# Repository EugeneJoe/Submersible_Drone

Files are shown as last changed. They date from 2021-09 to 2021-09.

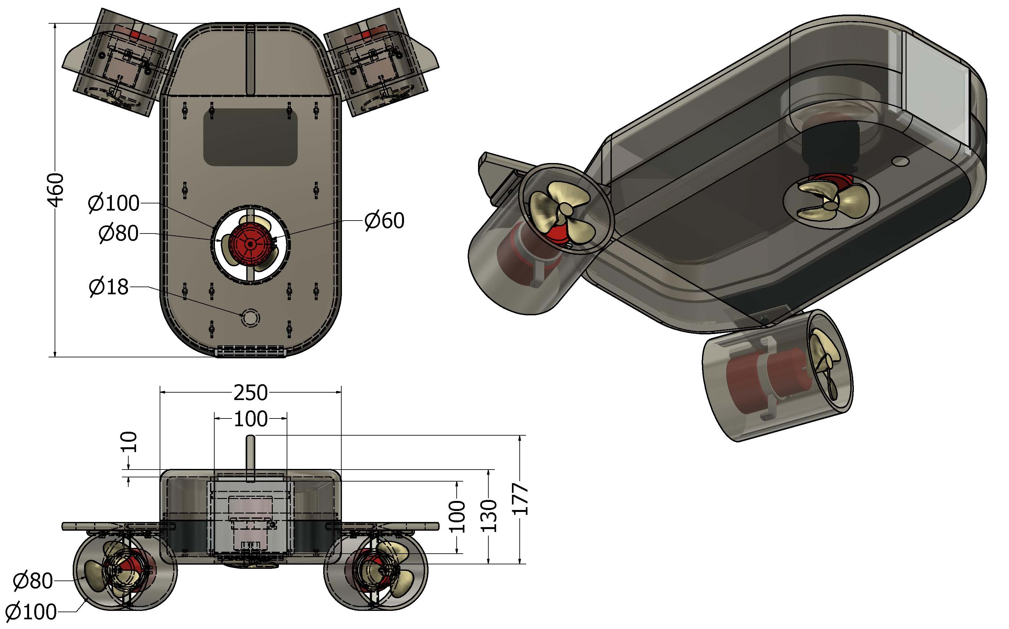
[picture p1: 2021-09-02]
Working_Drawings/JPG/Underwater ROV Assembly_Overall Dimensions.jpg

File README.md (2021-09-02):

# Submersible Drone Project

The files in this repository describe the different aspects that went into building our submersible, remote controlled drone. The drone was capable of underwater exploration through the use of a camera that sent back a live video feed of the submerged environment.
The different sections that went into the drone are:

1. An outer shell that is water-tight and housed all the components and positioned them appropriately.
2. Three motors from water pumps to provide vertical and horizontal thrust.
3. A raspberry pi controller through which the live video feed was transmitted and
propulsion signals were sent.
4. An arduino controller that received signals from the raspberry pi and drove the motors
through motor controller chips.
5. A raspberry pi camera module to capture video and transmit it back to the user. This could be viewed from a laptop.

The Final Report document contains a detailed report of how we went about designing and building the drone.

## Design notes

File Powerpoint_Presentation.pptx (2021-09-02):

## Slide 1

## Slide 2

Introduction: Objectives

Main Objective
  - Design and fabricate a hydrodynamic submersible vehicle capable of manoeuvring underwater environments and capturing videos and images

Specific Objectives
In order to achieve the above main objective, the following specific objectives must be satisfied:
1. To design and fabricate a water-tight hull of the ROV, keeping in mind hydrodynamics and strength of the mechanical design.
2. To design and fabricate the propulsion and pitch control system of the ROV.
3. To design the power delivery circuit to the electrical components in the ROV.
4. To design and implement the algorithm that coordinates the functioning of the ROV.
5. To test the operation and performance of the ROV system modules, and eventually the entire system operation with the modules working in tandem.

## Production Plan

Week | Tasks/ Activities | Materials Required | Special equipment | Simultaneous/ Concurrent activities | Status/ Remarks
5 | Assembly of live stream equipment Testing the live video stream | Raspberry pi camera module Raspberry pi microcontroller Display unit CAT 6 Cable | | | Complete
6 | Assembly of the power circuit: Acquisition of power supply unit Acquisition of terminal block and buck converter. Acquisition of CAT 6 cable Assembling the above components | CAT 6 Cable Power supply unit Buck converter | | | Power supply + Buck Converter acquired. Acquisition of cables underway.

## Production Plan

Week | Tasks/ Activities | Materials Required | Special equipment | Simultaneous/ Concurrent activities | Status/ Remarks
7 | Modification of Bilge pumps: Marking the housing where it needs to be cut. Cutting around the entire impeller housing being careful not to cut to deep into the motor casing, then discarding it. Prying the impeller off to expose the motor shaft. | 3No. Bilge pumps | Hobby Saw | | Complete
8 | Assembly of the motor control circuit Acquisition of materials required Connection to power circuit Testing the motor control for propulsion and pitch motors | Modified Bilge Pump Motors Dual channel H-bridge DC motor drivers Raspberry pi Microcontroller Jumper cables | | | Motor drivers – acquired.

## Production Plan

Week | Tasks/ Activities | Materials Required | Special equipment | Simultaneous/ Concurrent activities | Status/ Remarks
9 | 3D Print the mechanical structure of the ROV - Outer hull, propeller shrouds, propellers, motor support brackets. | Polyactic Acid (PLA) | 3D Printer | | Ongoing
10 | Machining of camera sight glass | Glass (108 × 106 × 3 mm) | | | Complete
11 | Assembly of the different components of the mechanical structure | Acetone / Epoxy / Cyanoacrylate Superglue / Solvent cement M5 × 10 set screws (6No.) M5 × 12 set screws (8No.) M5 Lock nuts (9No.) | | i) Fine tuning motor control
12 | Test of the complete U-ROV assembly and fine tuning its operation

## Methodology – Revised Mechanical Design - Exploded View

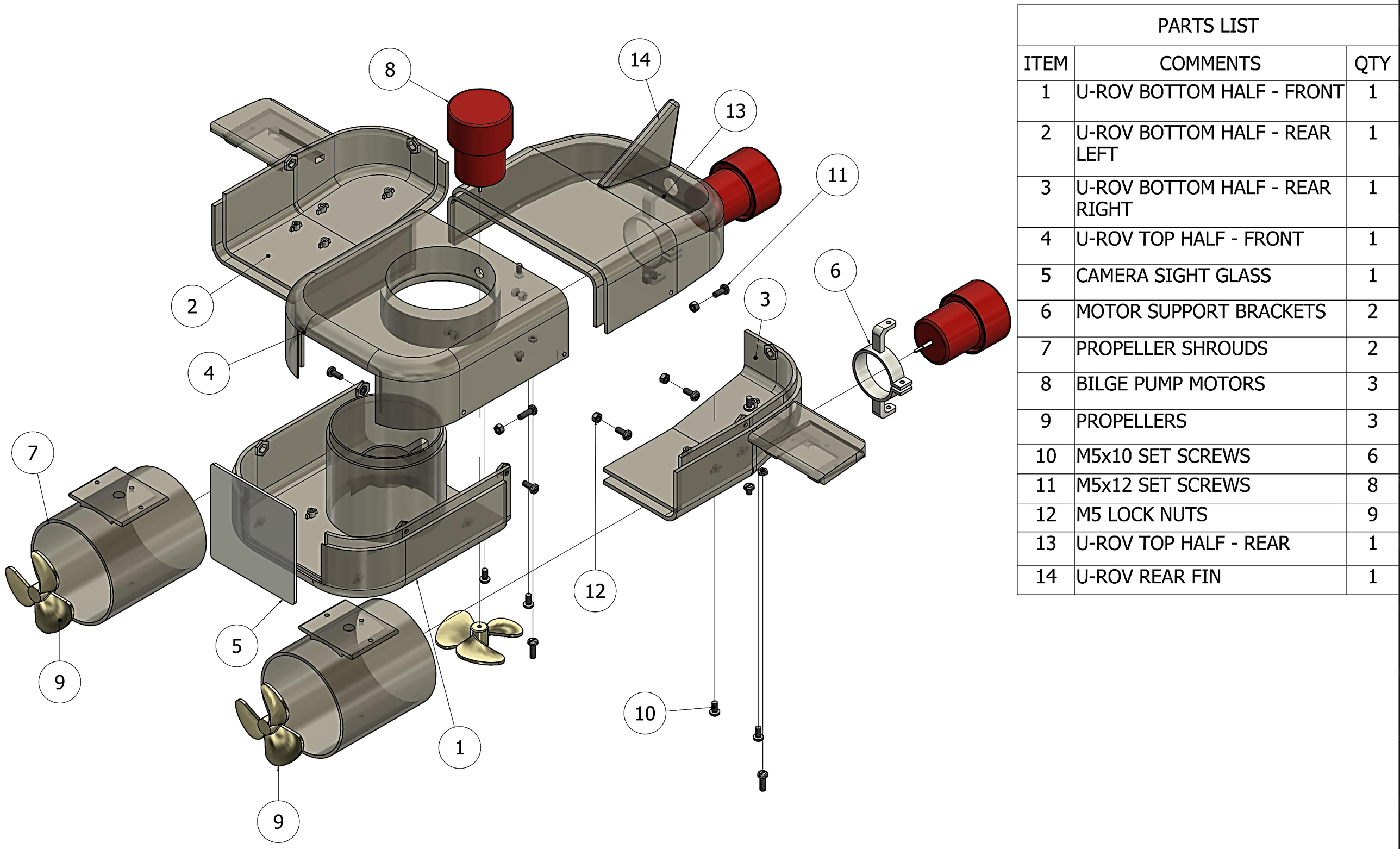
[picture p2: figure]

## Methodology – Flowchart

START

LIVESTREAM AUTOMATICALLY ACTIVATED

PITCH THRUSTER TRIGGERED

DESIRED DEPTH REACHED?

PITCH THRUSTER DEACTIVATED

FORWARD (F) / BACKWARD (B) MOTION?

c

F

B

NO

THRUSTER CLOCKWISE MOTION TRIGGERED

THRUSTER COUNTERCLOCKWISE MOTION TRIGGERED

YES

A

## Methodology – Flowchart

A

B

TURN LEFT(L) / RIGHT(R)?

RESURFACE?

PITCH THRUSTER REVERSED

END

N

C

L

R

Y

LEFT THRUSTER SPEED DECREASED

RIGHT THRUSTER SPEED DECREASED

B

## Control Module

  - Gamepad connected to laptop to which it sends signals based on user input.
  - Signal sent from joystick includes:
    - Direction of motion i.e ‘F’ for Forward, ‘R’ for Right.
    - Speed value to be passed to motor as PWM value:
      - Joystick input range (0-1) mapped to PWM values (0-255)
  - Laptop connected to Raspberry Pi as client with Pi acting as server.
  - Raspberry Pi receives Gamepad signal from laptop.
  - Raspberry pi sends signal to Arduino through Serial Connection.
  - Arduino actuates motors based on received signal.

## Budget

S/No | Item | Specifications | Qty | Units | Material | Estimated Unit Cost | Total Cost
1 | Raspberry pi camera module** | | 1 | Pieces | | 3,500 | 3,500*
2 | Raspberry pi** | | 1 | Pieces | | 6,000 | 6,000*
3 | Electric Bilge Pump | 1100 GPH, 12V, 3A | 3 | Pieces | | 1,836 | 5,508
4 | DC motor drivers | 3V-36V, 15A Dual Channel H-bridge | 2 | Pieces | | 1,838 | 3,676
5 | CAT6 cable | | 6 | Length (m) | | 70 | 420
6 | CAT6 cable end connectors | | 2 | Pieces | | 10 | 20
7 | Buck converter | LM2596HVS – 60V, 3A | 1 | Pieces | | 400 | 400

## Budget

S/No. | Item | Specifications | Qnty | Units | Material | Estimated Unit Cost | Total Cost
8 | LED Ring Lights | 61mm OD, 52mm ID | 1 | Pieces | | 1,707 | 1,707
9 | Set screws | M5×10 | 6 | Pieces | | 10 | 60
10 | Set screws | M5×12 | 8 | Pieces | | 10 | 80
11 | Fuse | 10A | 3 | Pieces | | 130 | 390
12 | Glass | 106mm × 108mm × 3 mm | 1 | Pieces | | 200 | 200
13 | Waterproof Cable Glands | PG7 (12.5 mm OD), PG13.5 (20.4mm OD) | 4 | Pieces | | 150 | 600
14 | 3D Printing | | 1 | Item | PLA | 20,000 | 20,000
Total Estimated Cost | | | | | | | 33,061
Subtotal Currently Spent | | | | | | | 20,311

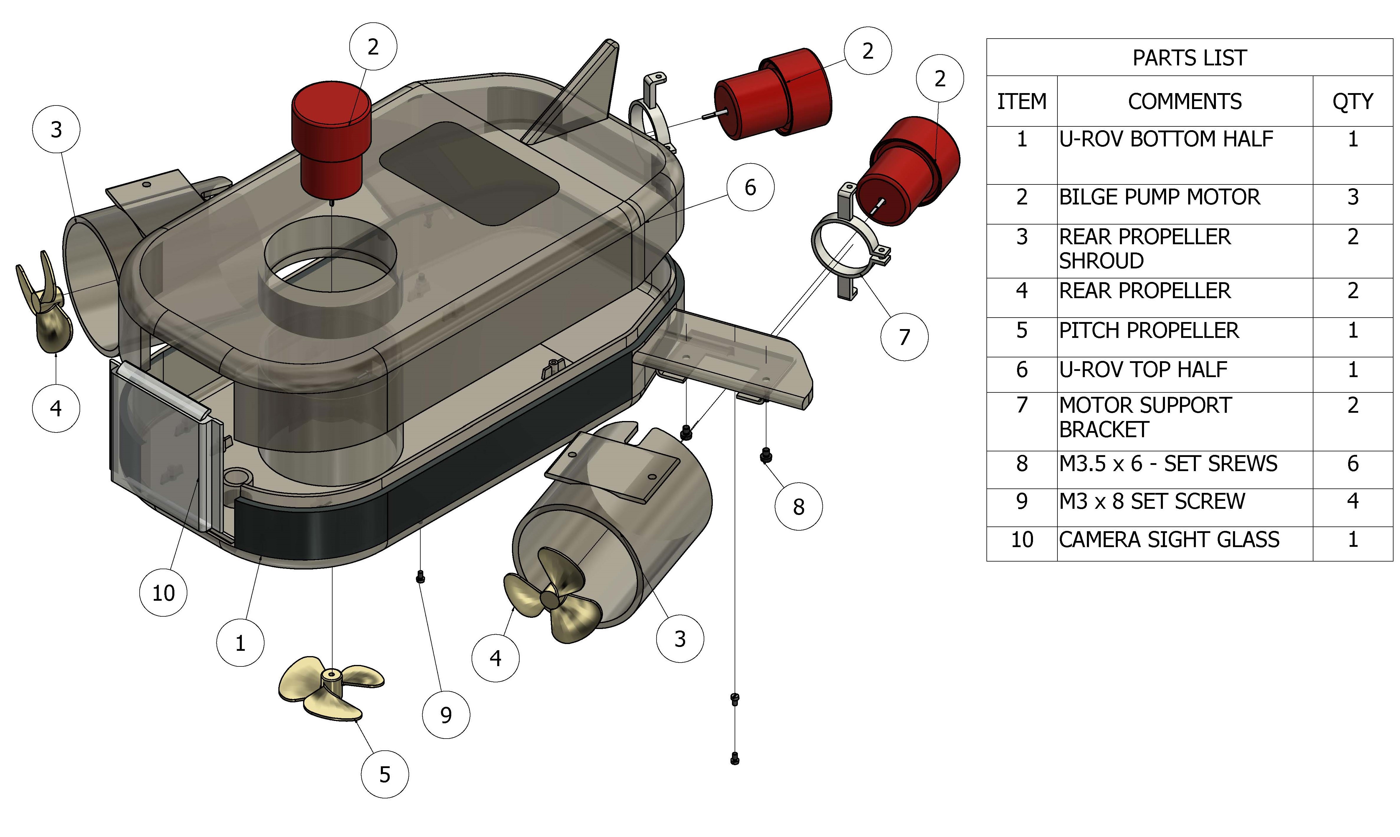
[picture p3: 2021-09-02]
Working_Drawings/PDF + DWG/EXPLODEDVIEW2.jpg

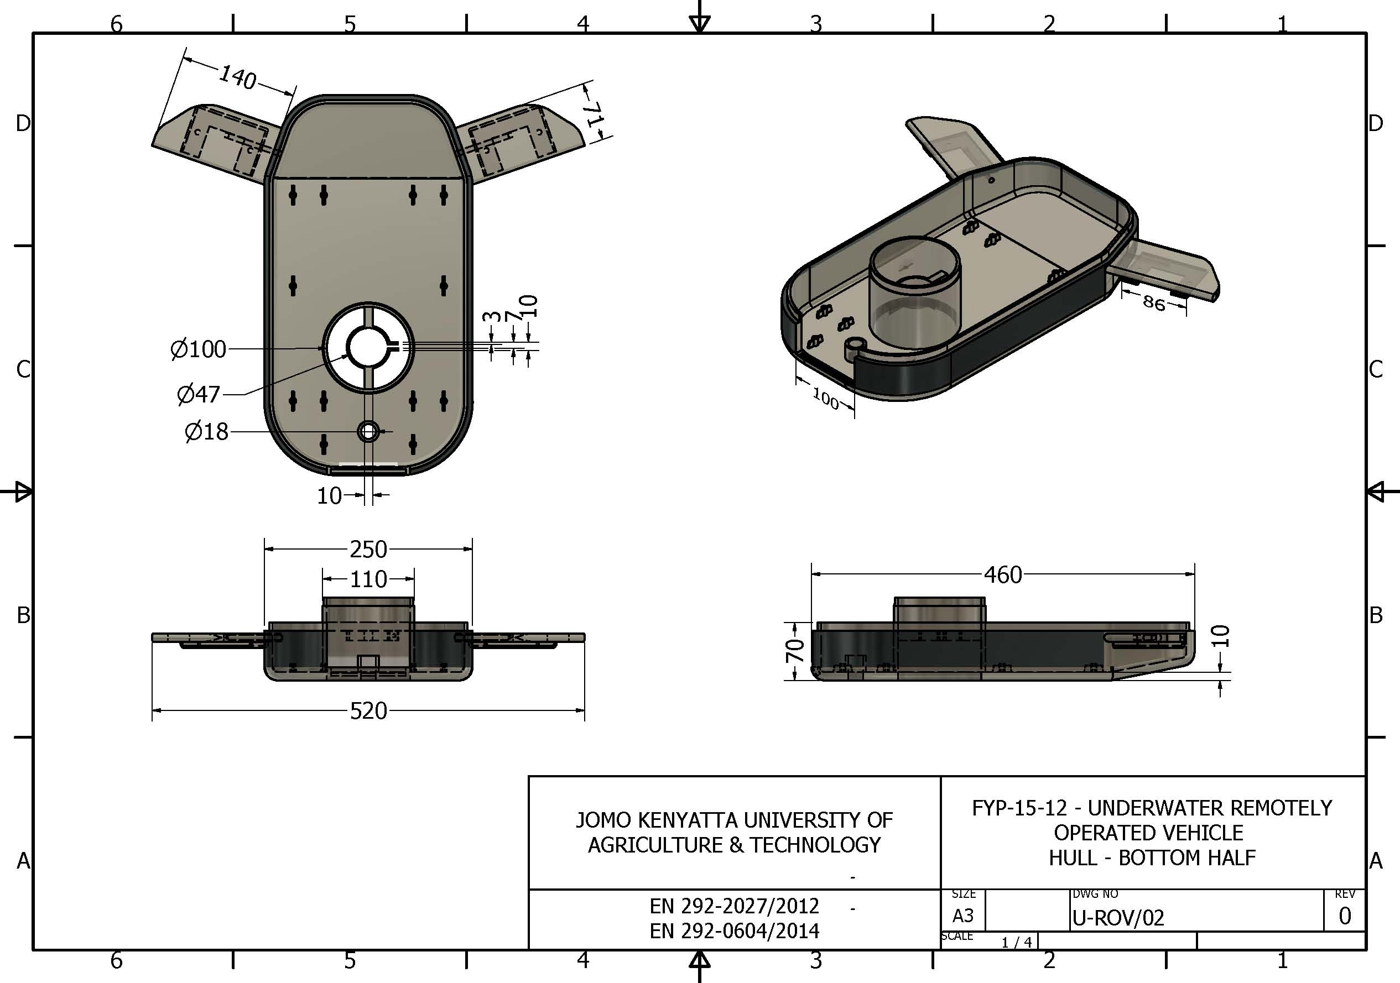
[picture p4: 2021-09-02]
Working_Drawings/PDF + DWG/HULL - BOTTOM HALF.jpg

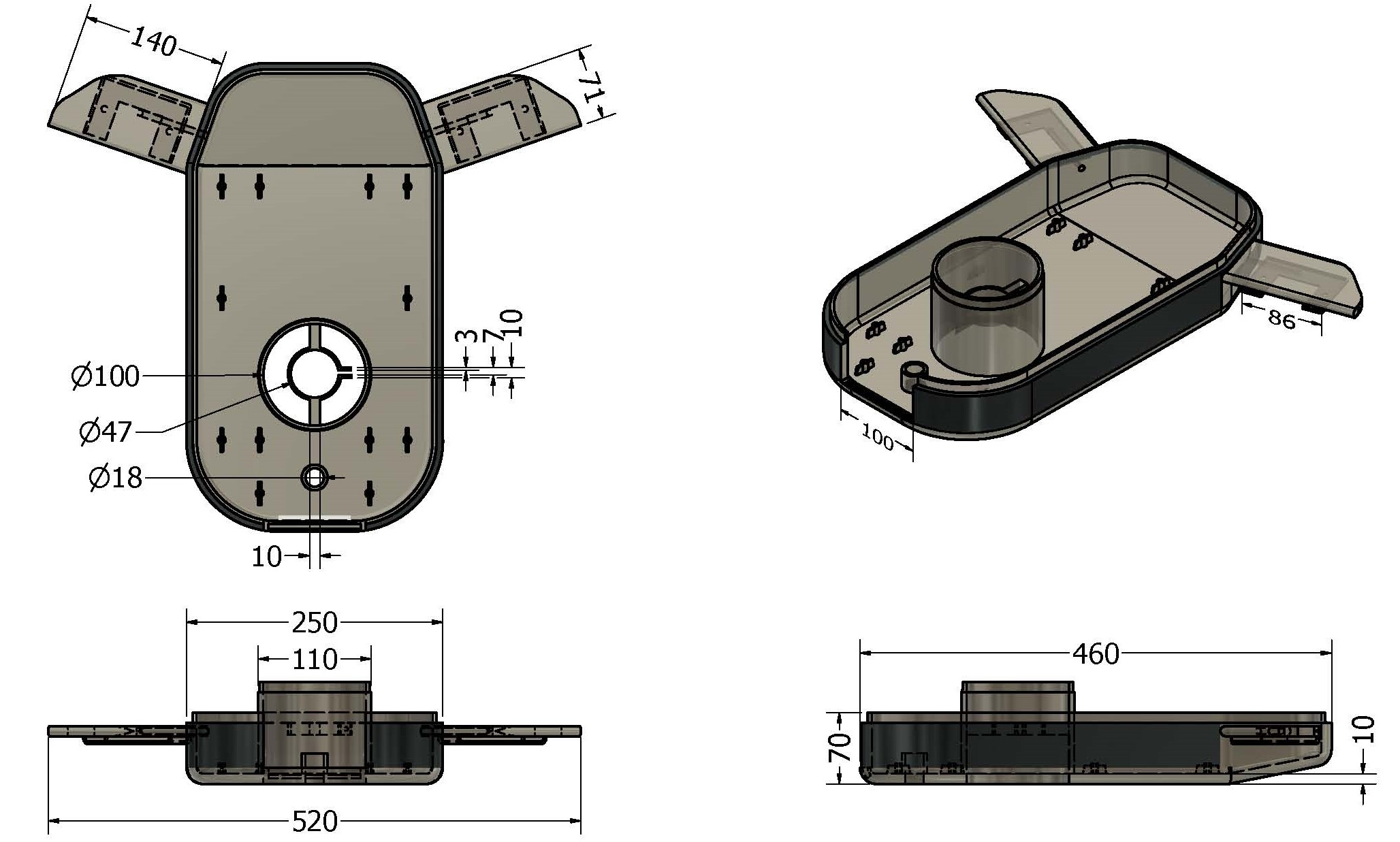
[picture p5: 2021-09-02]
Working_Drawings/JPG/U-ROV_Hull_BottomHalf3.0.jpg

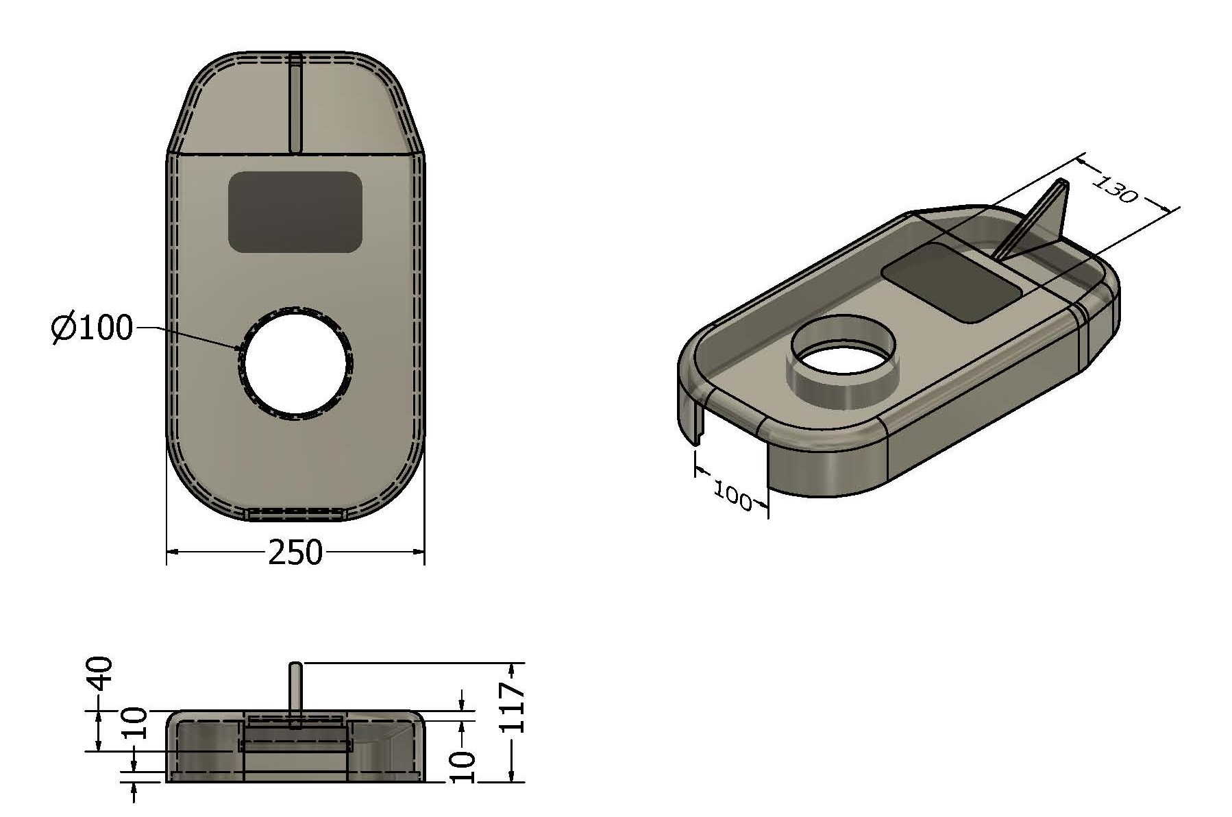
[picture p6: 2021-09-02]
Working_Drawings/JPG/U-ROV_Hull_Top Half3.0.jpg

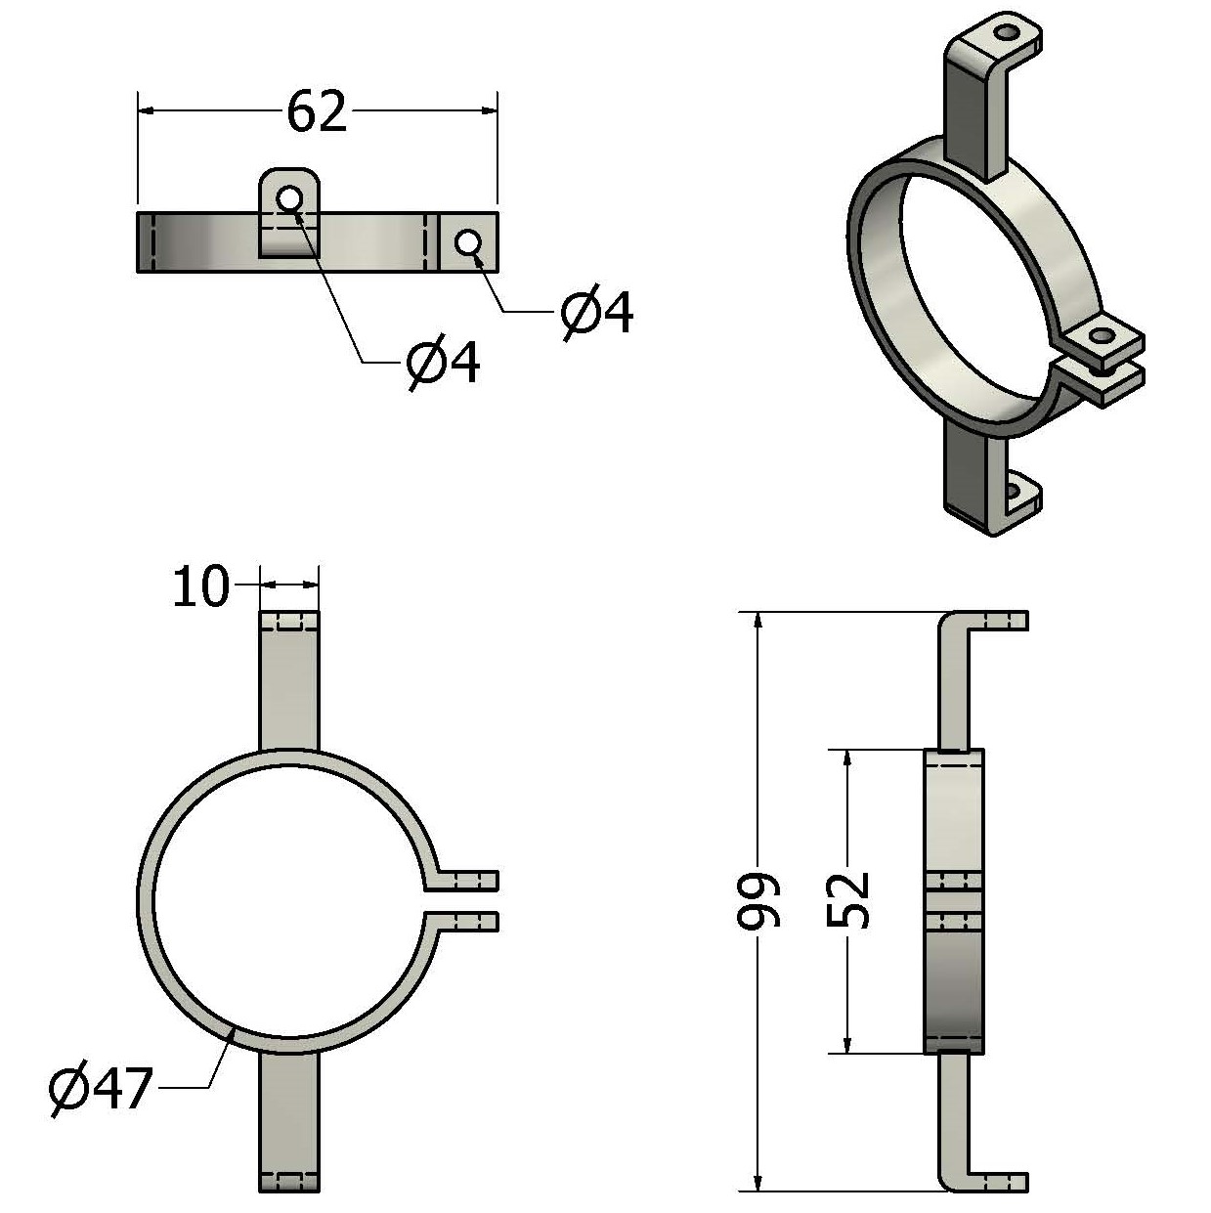
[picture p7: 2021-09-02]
Working_Drawings/JPG/SupportBracket_v2_BilgePumpMotor.jpg

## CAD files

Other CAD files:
Working_Drawings/PDF + DWG/U-ROV_Assembly_PartsLabelled.dwg
Working_Drawings/PDF + DWG/Underwater ROV Assembly_Overall Dimensions.dwg
Working_Drawings/PDF + DWG/U-ROV_Assembly_Exploded_WorkingDrawing-1.dwg
Working_Drawings/PDF + DWG/ROV Hull_Top Half 3.0.dwg
Working_Drawings/PDF + DWG/ROV Hull_Bottom Half 3.0.dwg
Working_Drawings/PDF + DWG/SupportBracket_v2_BilgePumpMotor.dwg
Working_Drawings/PDF + DWG/Propeller_Shroud.dwg
Working_Drawings/PDF + DWG/Rear Thruster 2.0.dwg
Working_Drawings/OldVersions/Underwater ROV Assembly_Overall Dimensions.0001.dwg
Working_Drawings/OldVersions/U-ROV_Assembly_Exploded_WorkingDrawing-1.0004.dwg
Working_Drawings/PDF + DWG/OldVersions/U-ROV_Assembly_Exploded_WorkingDrawing-1.0007.dwg
Working_Drawings/PDF + DWG/OldVersions/Underwater ROV Assembly_Overall Dimensions.0005.dwg
Working_Drawings/PDF + DWG/OldVersions/U-ROV_Assembly_PartsLabelled.0005.dwg
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

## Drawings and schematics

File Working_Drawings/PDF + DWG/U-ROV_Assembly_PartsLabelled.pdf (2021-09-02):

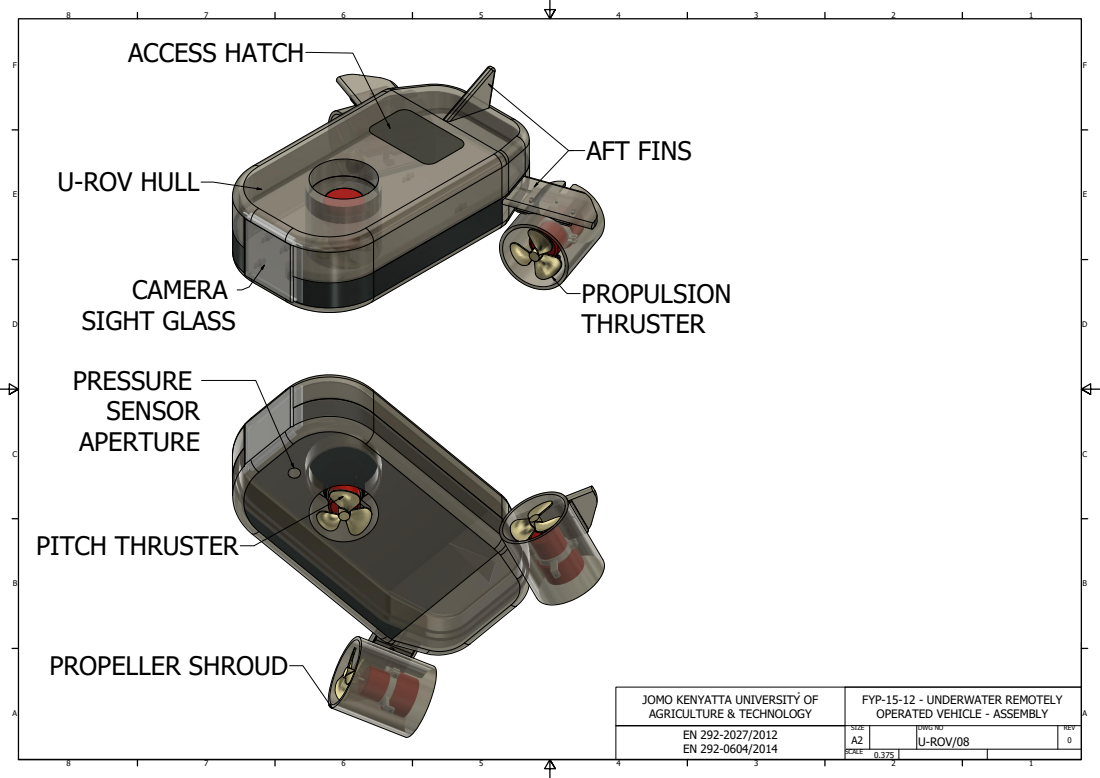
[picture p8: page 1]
U-ROV HULL; ACCESS HATCH; PITCH THRUSTER; SIGHT GLASS; AFT FINS; PROPELLER SHROUD

JOMO KENYATTA UNIVERSITY OF AGRICULTURE & TECHNOLOGY | FYP-15-12 - UNDERWATER REMOTELY OPERATED VEHICLE - ASSEMBLY

EN 292-2027/2012 EN 292-0604/2014 | SIZE A2 | DWG NO U-ROV/08 | REV 0

SCALE 0.375

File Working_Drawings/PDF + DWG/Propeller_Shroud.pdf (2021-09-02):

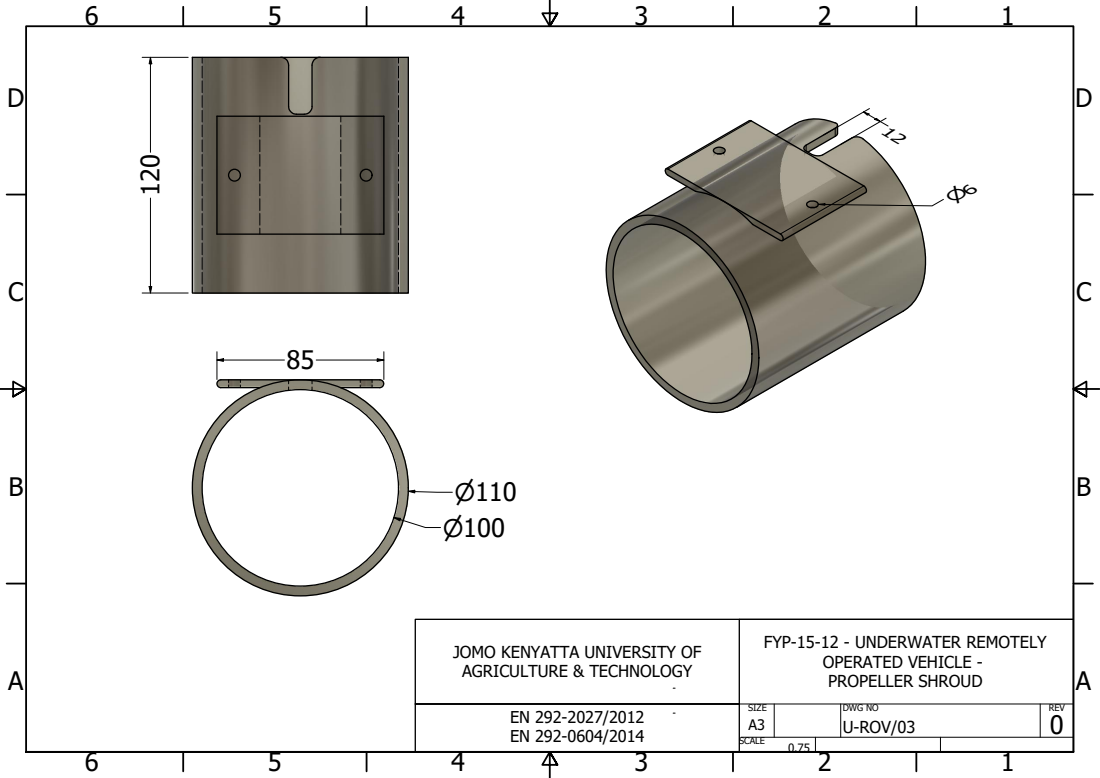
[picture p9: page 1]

JOMO KENYATTA UNIVERSITY OF AGRICULTURE & TECHNOLOGY | FYP-15-12 - UNDERWATER REMOTELY OPERATED VEHICLE -PROPELLER SHROUD

EN 292-2027/2012 EN 292-0604/2014 | SIZE A3 | DWG NO U-ROV/03 | REV 0

SCALE 0.75

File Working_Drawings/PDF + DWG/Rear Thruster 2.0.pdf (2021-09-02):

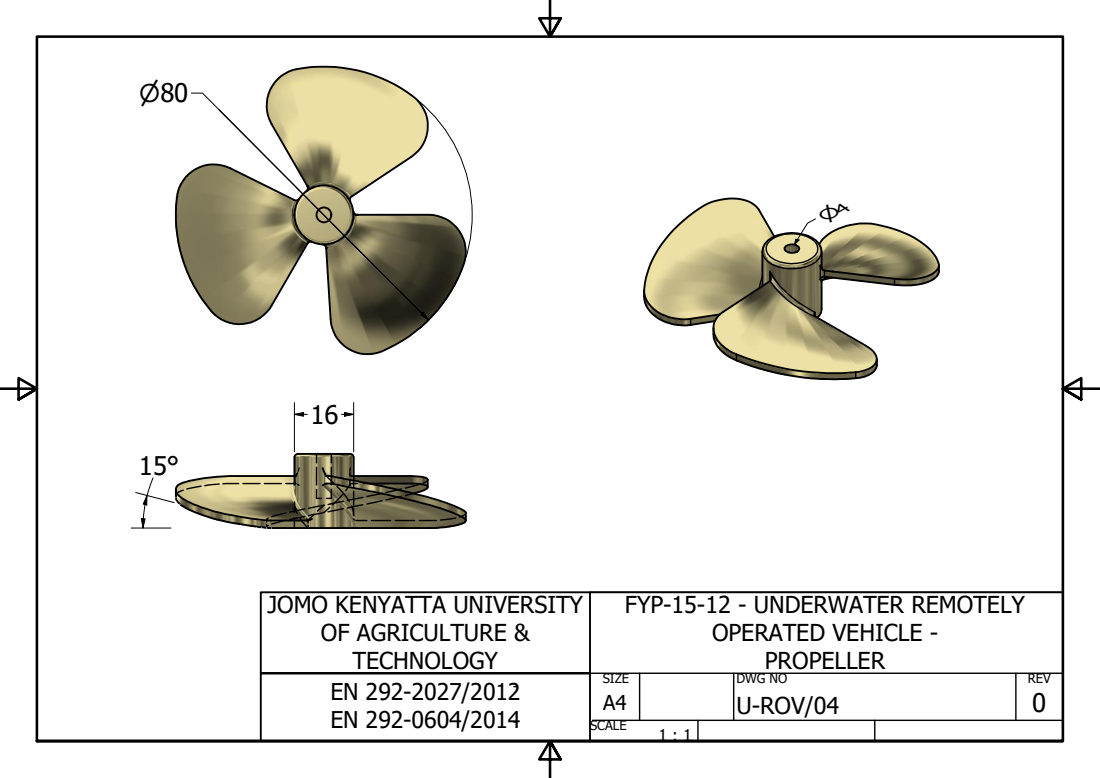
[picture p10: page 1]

JOMO KENYATTA UNIVERSITY OF AGRICULTURE & TECHNOLOGY | FYP-15-12 - UNDERWATER REMOTELY OPERATED VEHICLE -PROPELLER

EN 292-2027/2012 EN 292-0604/2014 | SIZE A4 | DWG NO U-ROV/04 | REV 0

SCALE 1 : 1

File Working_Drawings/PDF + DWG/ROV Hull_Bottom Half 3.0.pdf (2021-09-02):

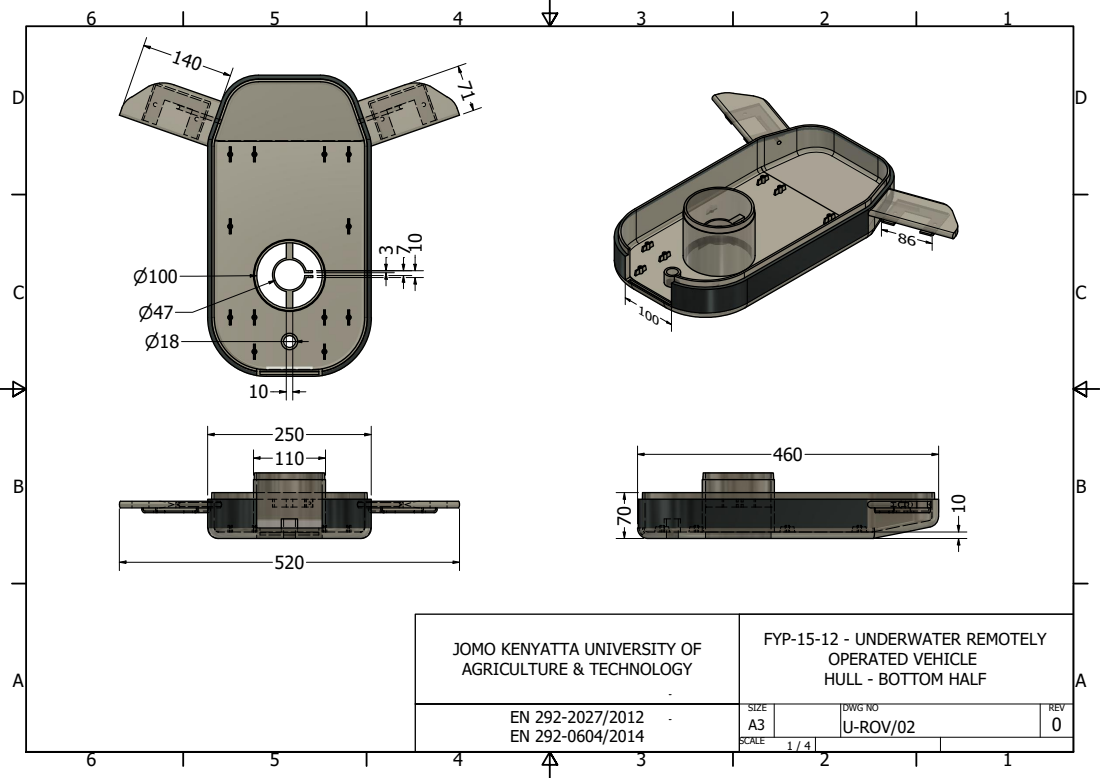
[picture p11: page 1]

JOMO KENYATTA UNIVERSITY OF AGRICULTURE & TECHNOLOGY | FYP-15-12 - UNDERWATER REMOTELY OPERATED VEHICLE HULL - BOTTOM HALF

EN 292-2027/2012 EN 292-0604/2014 | SIZE A3 | DWG NO U-ROV/02 | REV 0

SCALE 1 / 4

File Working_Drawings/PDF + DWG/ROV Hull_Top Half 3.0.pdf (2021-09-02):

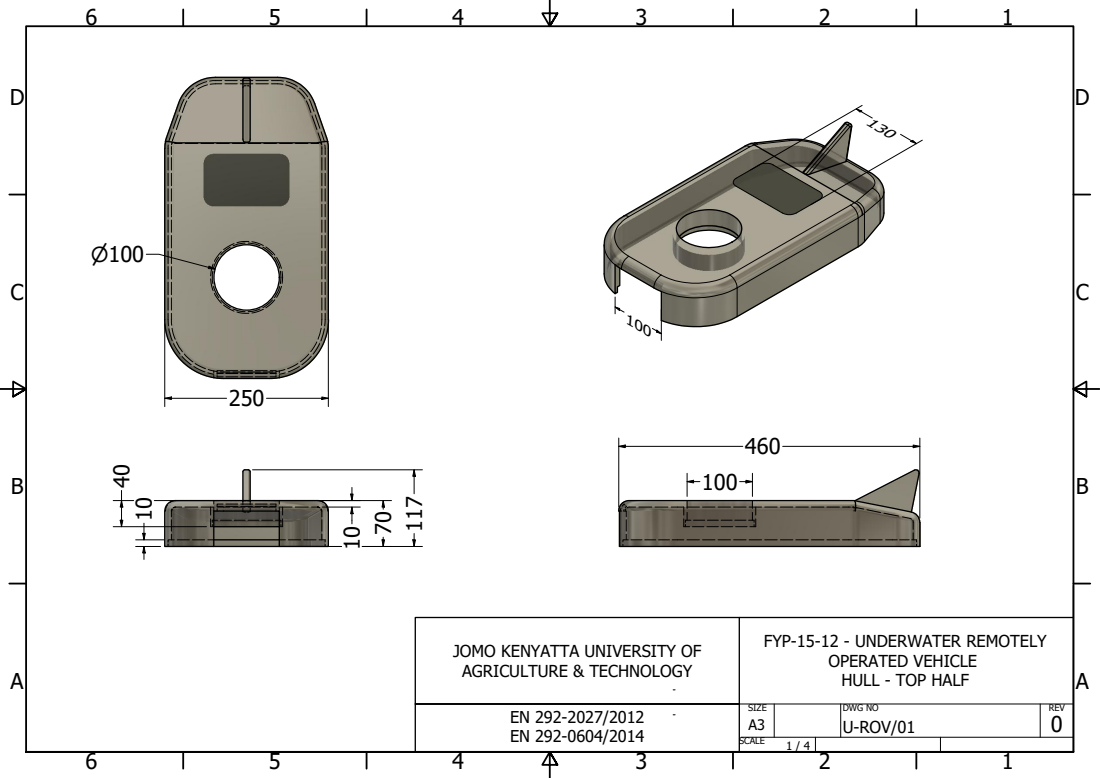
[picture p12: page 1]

JOMO KENYATTA UNIVERSITY OF AGRICULTURE & TECHNOLOGY | FYP-15-12 - UNDERWATER REMOTELY OPERATED VEHICLE HULL - TOP HALF

EN 292-2027/2012 EN 292-0604/2014 | SIZE A3 | DWG NO U-ROV/01 | REV 0

SCALE 1 / 4

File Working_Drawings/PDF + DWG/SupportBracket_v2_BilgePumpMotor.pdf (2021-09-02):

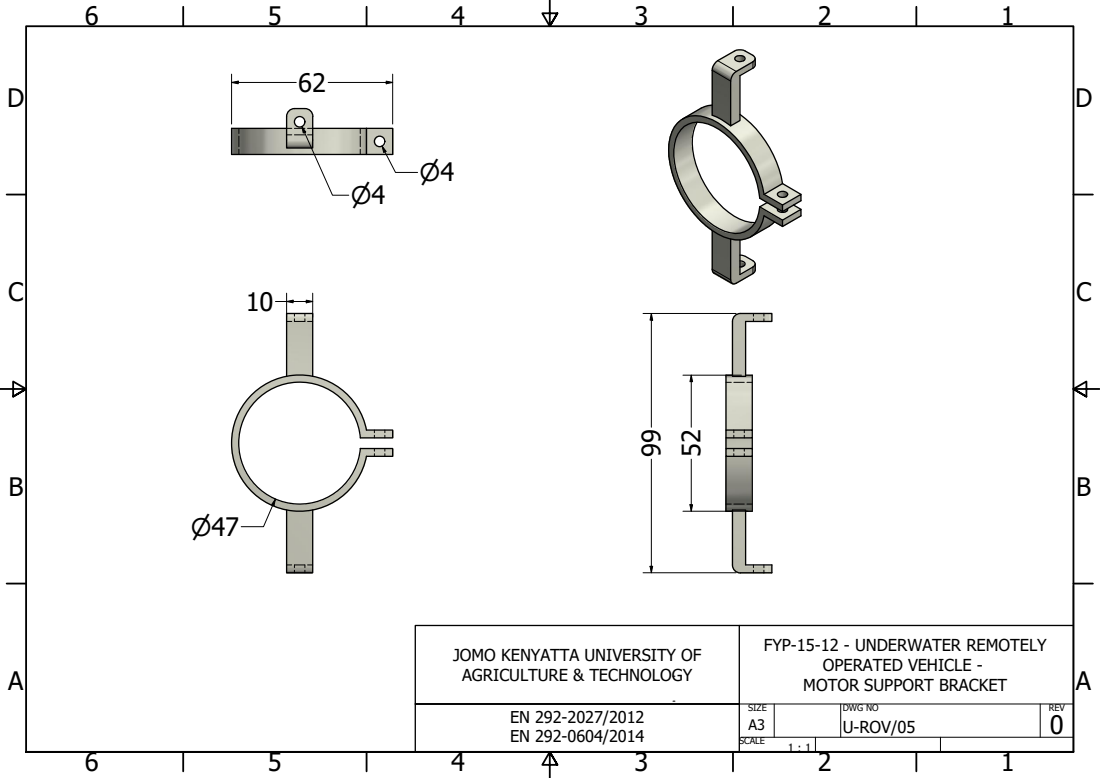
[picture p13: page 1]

JOMO KENYATTA UNIVERSITY OF AGRICULTURE & TECHNOLOGY | FYP-15-12 - UNDERWATER REMOTELY OPERATED VEHICLE -MOTOR SUPPORT BRACKET

EN 292-2027/2012 EN 292-0604/2014 | SIZE A3 | DWG NO U-ROV/05 | REV 0

SCALE 1 : 1

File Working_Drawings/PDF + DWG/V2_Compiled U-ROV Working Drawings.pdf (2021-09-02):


JOMO KENYATTA UNIVERSITY OF AGRICULTURE & TECHNOLOGY | FYP-15-12 - UNDERWATER REMOTELY OPERATED VEHICLE HULL - TOP HALF

EN 292-2027/2012 | SIZE A3 | DWG NO U-ROV/01 | REV

SCALE 1 / 4


JOMO KENYATTA UNIVERSITY OF AGRICULTURE & TECHNOLOGY | FYP-15-12 - UNDERWATER REMOTELY OPERATED VEHICLE HULL - BOTTOM HALF

SIZE | DWG NO | REV


JOMO KENYATTA UNIVERSITY OF AGRICULTURE & TECHNOLOGY | FYP-15-12 - UNDERWATER REMOTELY OPERATED VEHICLE -PROPELLER SHROUD

SIZE | DWG NO | REV


JOMO KENYATTA UNIVERSITY OF AGRICULTURE & TECHNOLOGY | FYP-15-12 - UNDERWATER REMOTELY OPERATED VEHICLE -PROPELLER

EN 292-2027/2012 | SIZE A4 | DWG NO U-ROV/04 | REV 0


JOMO KENYATTA UNIVERSITY OF AGRICULTURE & TECHNOLOGY | FYP-15-12 - UNDERWATER REMOTELY OPERATED VEHICLE -MOTOR SUPPORT BRACKET

SIZE | DWG NO | REV

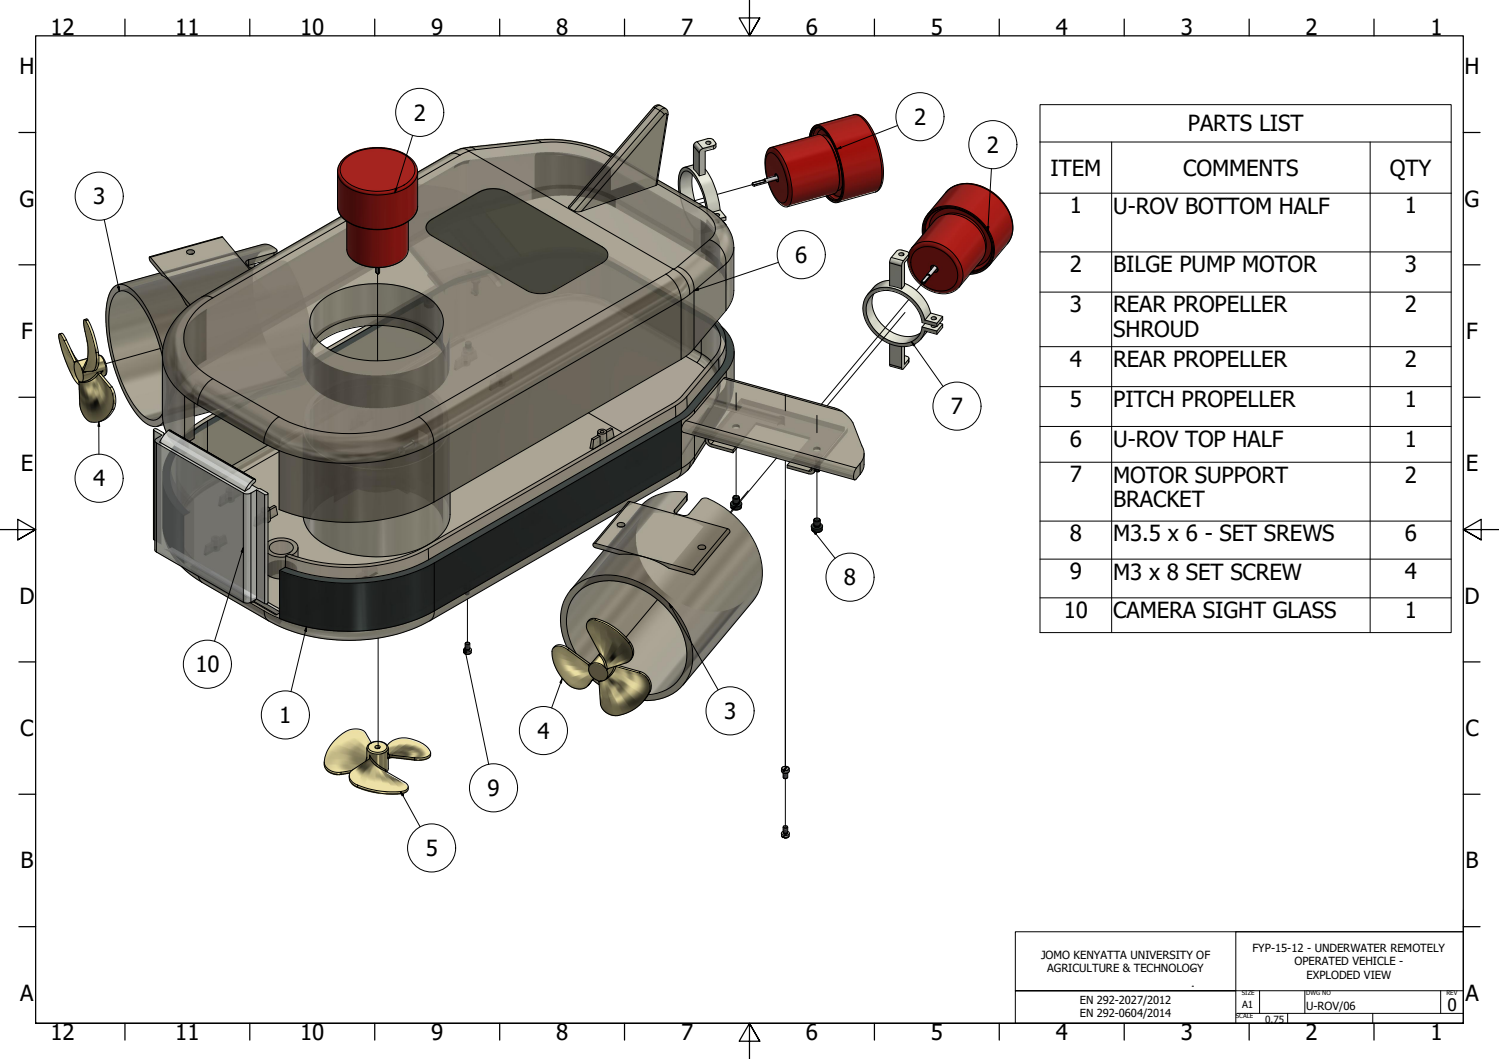
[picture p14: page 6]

I T E M | C O M M E N T S | Q TY
1 | U -R O V B O TT O M H A L F | 1

2 | B I L G E P U M P M O T O R | 3
34 | R E A R P R O P E L L E R S H R O U D | 2

R E A R P R O P E L L E R | 2
5 | P I T C H P R O P E L L E R | 1
6 | U -R O V T O P H A L F | 1
78 | M O T O R S U P P O RT B RA C K E T | 2

M 3 . 5 x 6 -S E T S R E W S | 6
9 | M 3 x 8 S E T S C R E W | 4
1 0 | C A M E RA S I G H T G LA S S | 1

J O M O K E N YATTA U N I V E R S I TY O F A G R I C U L T U R E & T E C H N O L O G Y | FY P -1 5 -1 2 -U N D E RW AT E R R E M O T E LY O P E RAT E D V E H I C L E -E X P L O D E D V I E W

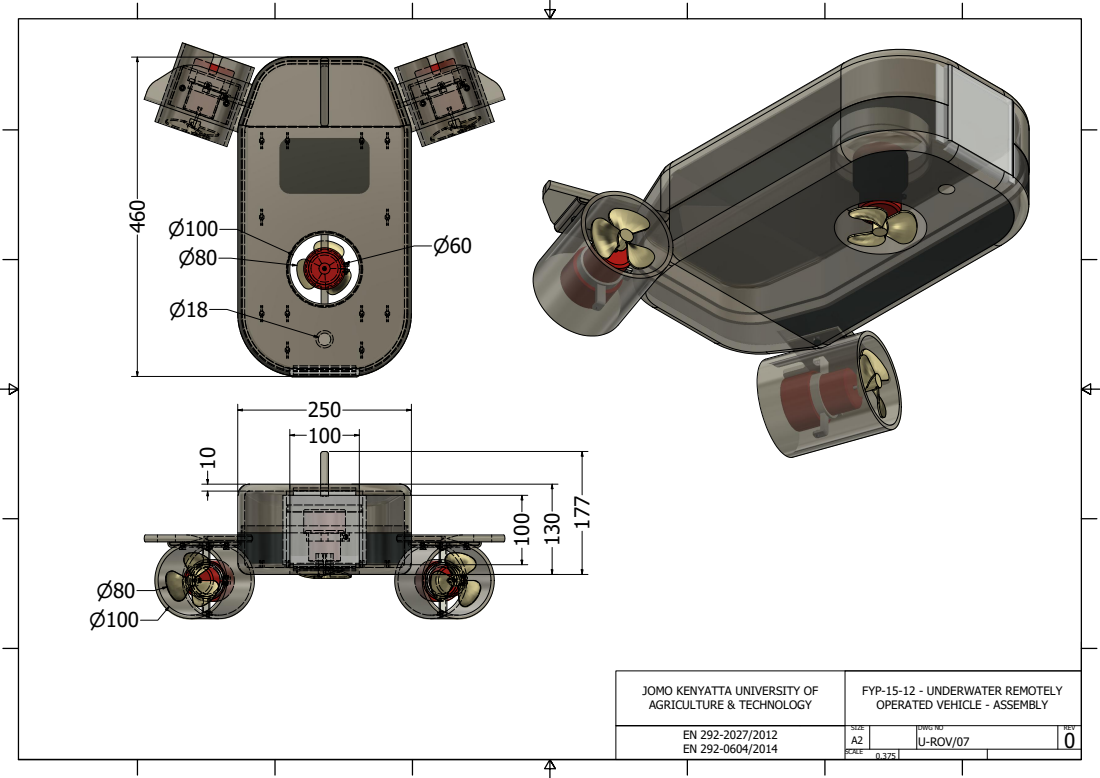
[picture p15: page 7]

JOMO KENYATTA UNIVERSITY OF AGRICULTURE & TECHNOLOGY | FYP-15-12 - UNDERWATER REMOTELY OPERATED VEHICLE - ASSEMBLY

SIZE | DWG NO | REV

U-ROV HULL; ACCESS HATCH; PITCH THRUSTER; SIGHT GLASS; AFT FINS; PROPELLER SHROUD

JOMO KENYATTA UNIVERSITY OF AGRICULTURE & TECHNOLOGY | FYP-15-12 - UNDERWATER REMOTELY OPERATED VEHICLE - ASSEMBLY

SIZE | DWG NO | REV

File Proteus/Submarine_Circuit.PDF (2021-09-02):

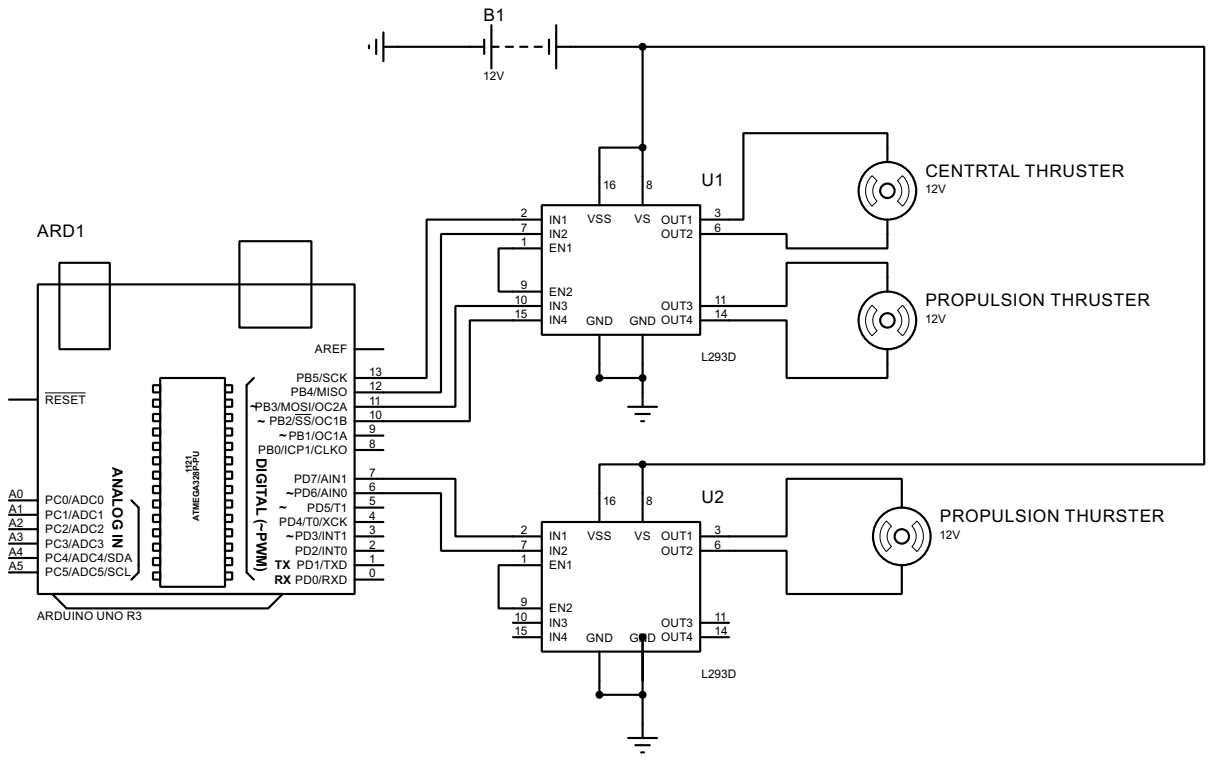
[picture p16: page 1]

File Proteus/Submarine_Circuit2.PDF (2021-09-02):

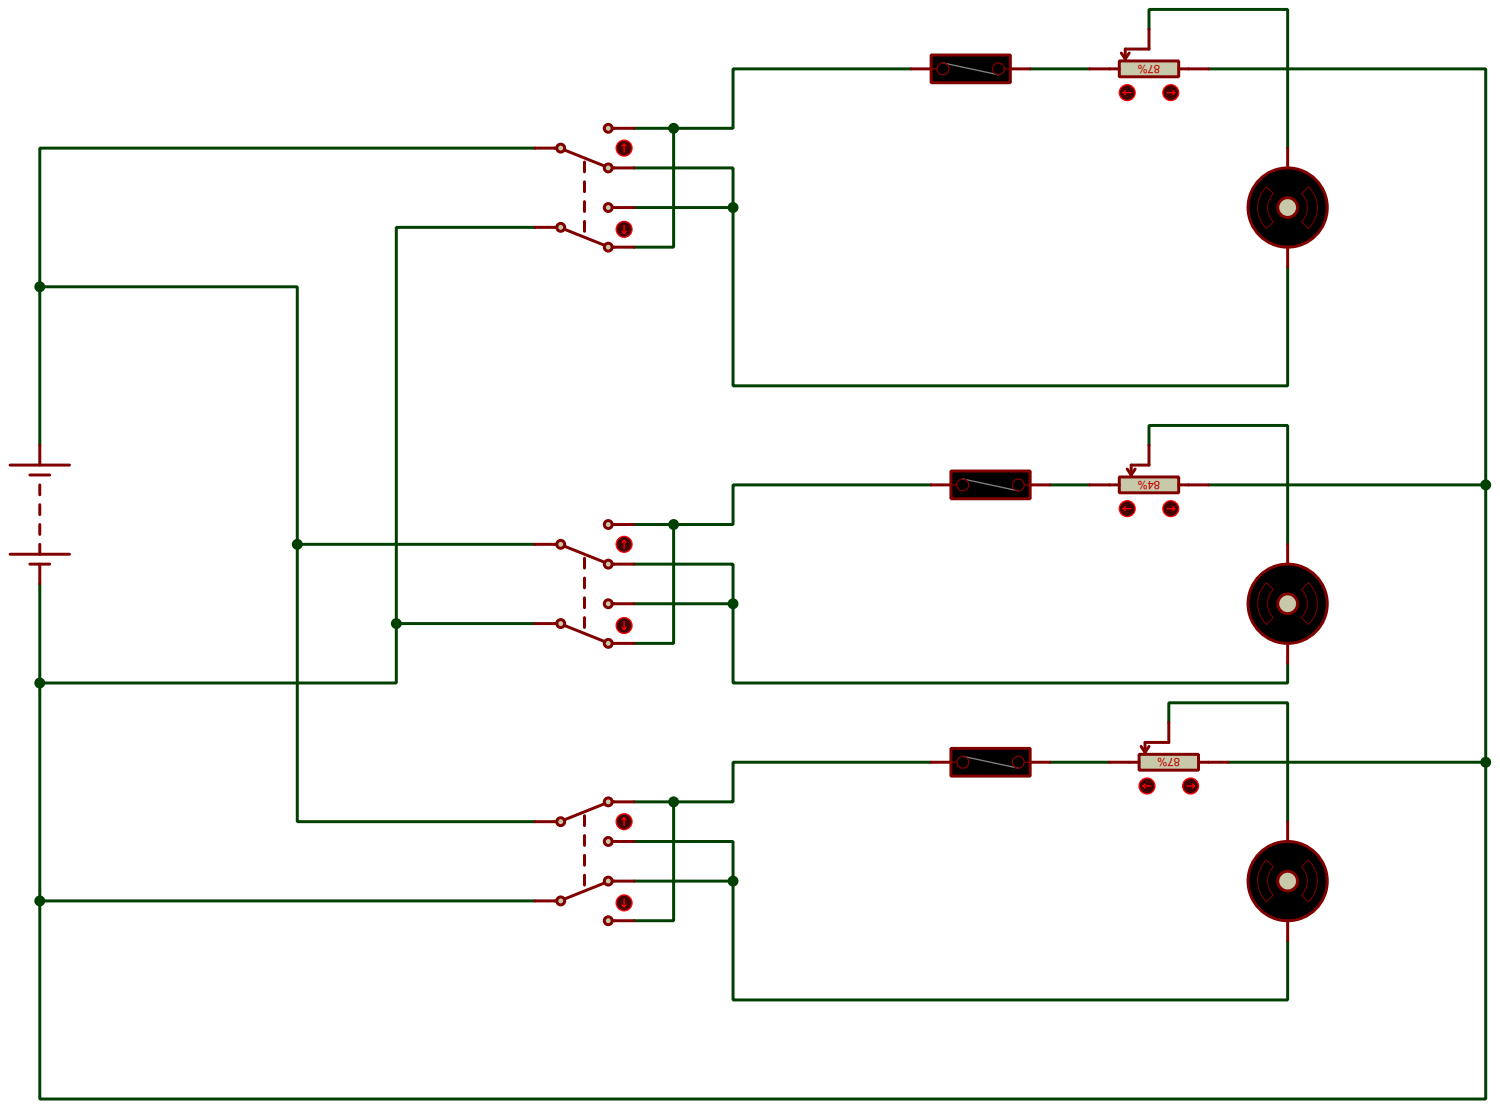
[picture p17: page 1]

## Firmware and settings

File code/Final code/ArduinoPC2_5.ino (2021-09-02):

//Enable Driver 2
int ENABLE1 = 8;
int ENABLE3 = 13;

//Motor1
int DIR1 = 9;
int PWM1 = 10;

//Motor 2
int DIR2 = 7;
int PWM2 = 6;

//Motor 3
int DIR3 = 12;
int PWM3 = 11;

//Input Read variables
const byte buffSize = 40;
char inputBuffer[buffSize];
const char startMarker = '<';
const char endMarker = '>';
byte bytesRecvd = 0;
boolean readInProgress = false;
boolean newDataFromPC = false;

char messageFromPC[buffSize] = {0};
char messageFromPC2[buffSize] = {0};
int newFlashInterval = 0;
int PWM_P = 0;
int PWM_S = 0;
int PWM_PP = 0;


unsigned long curMillis;
unsigned long prevReplyToPCmillis = 0;
unsigned long replyToPCinterval = 1000;

//=============

void setup() {
  Serial.begin(9600);
  
  pinMode(DIR2, OUTPUT);
  pinMode(PWM2, OUTPUT);
  pinMode(ENABLE1, OUTPUT);
  pinMode(DIR1, OUTPUT);
  pinMode(PWM1, OUTPUT); 
  digitalWrite(ENABLE1, HIGH);
  pinMode(DIR3, OUTPUT);
  pinMode(PWM3, OUTPUT);
  pinMode(ENABLE3, OUTPUT);
  digitalWrite(ENABLE3, HIGH);
  
    // tell the PC we are ready
  Serial.println("<Arduino is ready>");
}

//=============

void loop() {
  curMillis = millis();
  getDataFromPC(); //Read data from PC
  replyToPC();  //Send back received data to check for data corruption
  updateMotion();
}

//=============

void getDataFromPC() {

    // receive data from PC and save it into inputBuffer
    
  if(Serial.available() > 0) {

    char x = Serial.read();

      // the order of these IF clauses is significant
      
    if (x == endMarker) {
      readInProgress = false;
      newDataFromPC = true;
      inputBuffer[bytesRecvd] = 0;
      parseData();
    }
    
    if(readInProgress) {
      inputBuffer[bytesRecvd] = x;
      bytesRecvd ++;
      if (bytesRecvd == buffSize) {
        bytesRecvd = buffSize - 1;
      }
    }

    if (x == startMarker) { 
      bytesRecvd = 0; 
      readInProgress = true;
    }
  }
}

//=============
 
void parseData() {

    // split the data into its parts
    
  char * strtokIndx; // this is used by strtok() as an index
  
  strtokIndx = strtok(inputBuffer,",");      // get the first part - the string
  strcpy(messageFromPC, strtokIndx); // copy it to messageFromPC; direction - forward or backward
  
  strtokIndx = strtok(NULL, ","); // this continues where the previous call left off
  PWM_P = atoi(strtokIndx);     // convert this part to an integer

  strtokIndx = strtok(NULL, ","); // this continues where the previous call left off
  PWM_S = atoi(strtokIndx);     // convert this part to an integer

  strtokIndx = strtok(NULL, ","); // this continues where the previous call left off
  strcpy(messageFromPC2, strtokIndx);     // convert this part to an integer; direction - up or down

  strtokIndx = strtok(NULL, ","); // this continues where the previous call left off
  PWM_PP = atoi(strtokIndx);     // convert this part to an integer
}

//=============

void replyToPC() {

  if (newDataFromPC) {
    newDataFromPC = false;
    Serial.print("<Msg ");
    Serial.print(messageFromPC);
    Serial.print(" Primary PWM ");
    Serial.print(PWM_P);
    Serial.print(" Secondary PWM ");
    Serial.print(PWM_S);
    Serial.print(" Msg 2 ");
    Serial.print(messageFromPC2);
    Serial.print(" Pitch PWM ");
    Serial.print(PWM_PP);
    Serial.print(" Time ");
    Serial.print(curMillis >> 9); // divide by 512 is approx = half-seconds
    Serial.println(">");
  }
}

//============

void updateMotion() {
    if (strcmp(messageFromPC, "F") == 0){
      digitalWrite(DIR1, HIGH);
      analogWrite(PWM1, PWM_P);

      digitalWrite(DIR2, HIGH);
      analogWrite(PWM2, PWM_S);   
    }
    else if (strcmp(messageFromPC, "B") == 0){
      digitalWrite(DIR1, LOW);
      analogWrite(PWM1, PWM_P);

      digitalWrite(DIR2, LOW);
      analogWrite(PWM2, PWM_S);   
    }
    else if (strcmp(messageFromPC, "N") == 0){
      Stop();
    }
    if (strcmp(messageFromPC2, "U") == 0){
      digitalWrite(DIR3, HIGH);
      analogWrite(PWM3, PWM_PP);
    }
    else if (strcmp(messageFromPC2, "D") == 0){
      digitalWrite(DIR3, LOW);
      analogWrite(PWM3, PWM_PP);
    }
    else if (strcmp(messageFromPC2, "N") == 0){
      digitalWrite(DIR3, LOW);
      analogWrite(PWM3, 0);
    }
}  

//=============

void Stop(){
  digitalWrite(DIR1, LOW);
  analogWrite(PWM1, 0);

  digitalWrite(DIR2, LOW);
  analogWrite(PWM2, 0);
}

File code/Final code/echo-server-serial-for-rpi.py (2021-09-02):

import socket
import serial
import sys

#=====================================

def sendToArduino(sendStr):
  ser.write(sendStr) #serially send data to Arduino


#======================================

def recvFromArduino():
  global startMarker, endMarker
  
  ck = ""
  x = "z" # any value that is not an end- or startMarker
  byteCount = -1 # to allow for the fact that the last increment will be one too many
  
  # wait for the start character
  while  ord(x) != startMarker: 
    x = ser.read()
  
  # save data until the end marker is found
  while ord(x) != endMarker:
    if ord(x) != startMarker:
      ck = ck + x 
      byteCount += 1
    x = ser.read()
  
  return(ck) #string containing received data


#============================

def waitForArduino():

   # wait until the Arduino sends 'Arduino Ready' - allows time for Arduino reset
   # it also ensures that any bytes left over from a previous message are discarded
   
    global startMarker, endMarker
    
    msg = ""
    while msg.find("Arduino is ready") == -1:

      while ser.inWaiting() == 0:
        pass
        
      msg = recvFromArduino()

      print msg
      print
      
#======================================

def runTest(td):
  numLoops = len(td)
  waitingForReply = False

  n = 0
  while n < numLoops:

    teststr = td[n]

    if waitingForReply == False:
      sendToArduino(teststr)
      print "Sent from PC -- LOOP NUM: " + str(n) + " TEST STR: " + teststr
      waitingForReply = True

    if waitingForReply == True:

      while ser.inWaiting() == 0:
        pass
        
      dataRecvd = recvFromArduino()
      print "Reply Received:  " + dataRecvd
      n += 1
      waitingForReply = False

      print "==========="

##    time.sleep(5)

##Serial connection to Arduino set-up
serPort = "/dev/ttyACM0" #Port address of Arduino on the Pi
baudRate = 9600  #Set data transfer rate
ser = serial.Serial(serPort, baudRate)
print "Serial port " + serPort + " opened  Baudrate " + str(baudRate)


startMarker = 60 #'<'
endMarker = 62 #'>'
waitForArduino() #Wait for arduino to reset and acknowledge connection to PC


##Socket connection to PC
s = socket.socket(socket.AF_INET, socket.SOCK_STREAM)
address = ('192.168.137.2',21000)
s.bind(address) #Set up connection point for PC

s.listen(1)
while True:
    print 'waiting for a connection'
    conn, addr = s.accept() #Accept connection request from PC
    try:
        print('Connection from ', addr)
        while True:
            data = conn.recv(1024)
            print('Received ', data)
            if data:
                print 'Sending data back'
                conn.sendall(data)
                testData = []
                testData.append(data)
                runTest(testData) #send data to arduino
            else:
                print 'No more data'
                break
    finally:
        conn.close()

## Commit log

2021-09-02 Electrical Circuit Files
2021-09-02 Structural Drawings
    [Bilge-pump-motor.ipt, Bilge-pump.0003.ipt, Bilge-pump.ipt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]
2021-09-02 Powerpoint Presentation
